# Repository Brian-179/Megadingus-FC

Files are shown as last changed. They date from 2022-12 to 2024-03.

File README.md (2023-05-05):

# Megadingus-FC
Megadingus flight controllers/altimeters

(OUTDATED) FC1.5: Mostly tested, i2C bus is having an error, SPI untested and UART/USB works fine.

FC2.1: Fully ground tested but not flight proven under TVC. TVC flight imminent.

3 pyro channels

WiFi (ESP8266)

Main MCU is an RP2040

Main power connector is an XT30 (2-5S, 6S if you're willing to take the risk)

USB Mini B port

BMI088 IMU, BME280 Barometer

3 servo outputs

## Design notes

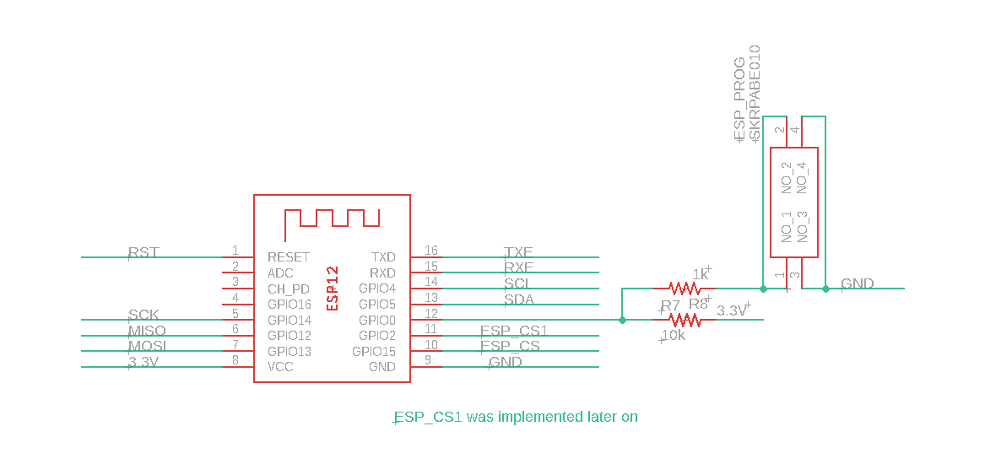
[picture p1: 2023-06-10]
fc2.1/fc2.1_8266/Screenshot 2023-06-04 113441.png

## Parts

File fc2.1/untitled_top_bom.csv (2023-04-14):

Comment | Designator | Footprint | LCSC Part #
ABLS-12.000MHZ-B4-T | F1 | HC/49US-(AT49)_1
ASMB-KTF0-0A306 | LED1 | ASMBKTF00A306
BME280 | HM1 | BME280
BMI088 | IC2 | BMI088
GDH04S04 | S1 | SOIC127P813X256-8N
L7805CDT-TR | IC5 | L7805CDTTR
RP2040 | U1 | QFN-56
SKRPABE010 | ESP_PROG RP2040-PROG RST | SKRPABE010

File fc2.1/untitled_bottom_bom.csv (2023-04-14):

Comment | Designator | Footprint | LCSC Part #
0 | R12 R14 R16 R17 | R2512
1k | R3 R6 R8 R10 | M0805
1uf | C6 | C0805
10k | R4 R5 R7 R9 R11 R13 R15 | M0805
10uf | C1 C5 | C0805
27p | C2 C3 | C0805
30 | R18 | M0805
33 | R1 R2 | M0805
47 | R19 | M0805
100 | R20 | M0805
503398-1892 | J1 | 503398-1892
FT231XS-R | IC3 | SOP64P599X175-20N
SISH536DN-T1-GE3 | Q1 Q2 Q5 | SQSA80ENWT1_GE3
TC1264-3.3VDBTR | IC1 | SOT230P700X180-4N
W25Q128JVSIQ_TR | L1 L2 | SOIC127P780X195-8N

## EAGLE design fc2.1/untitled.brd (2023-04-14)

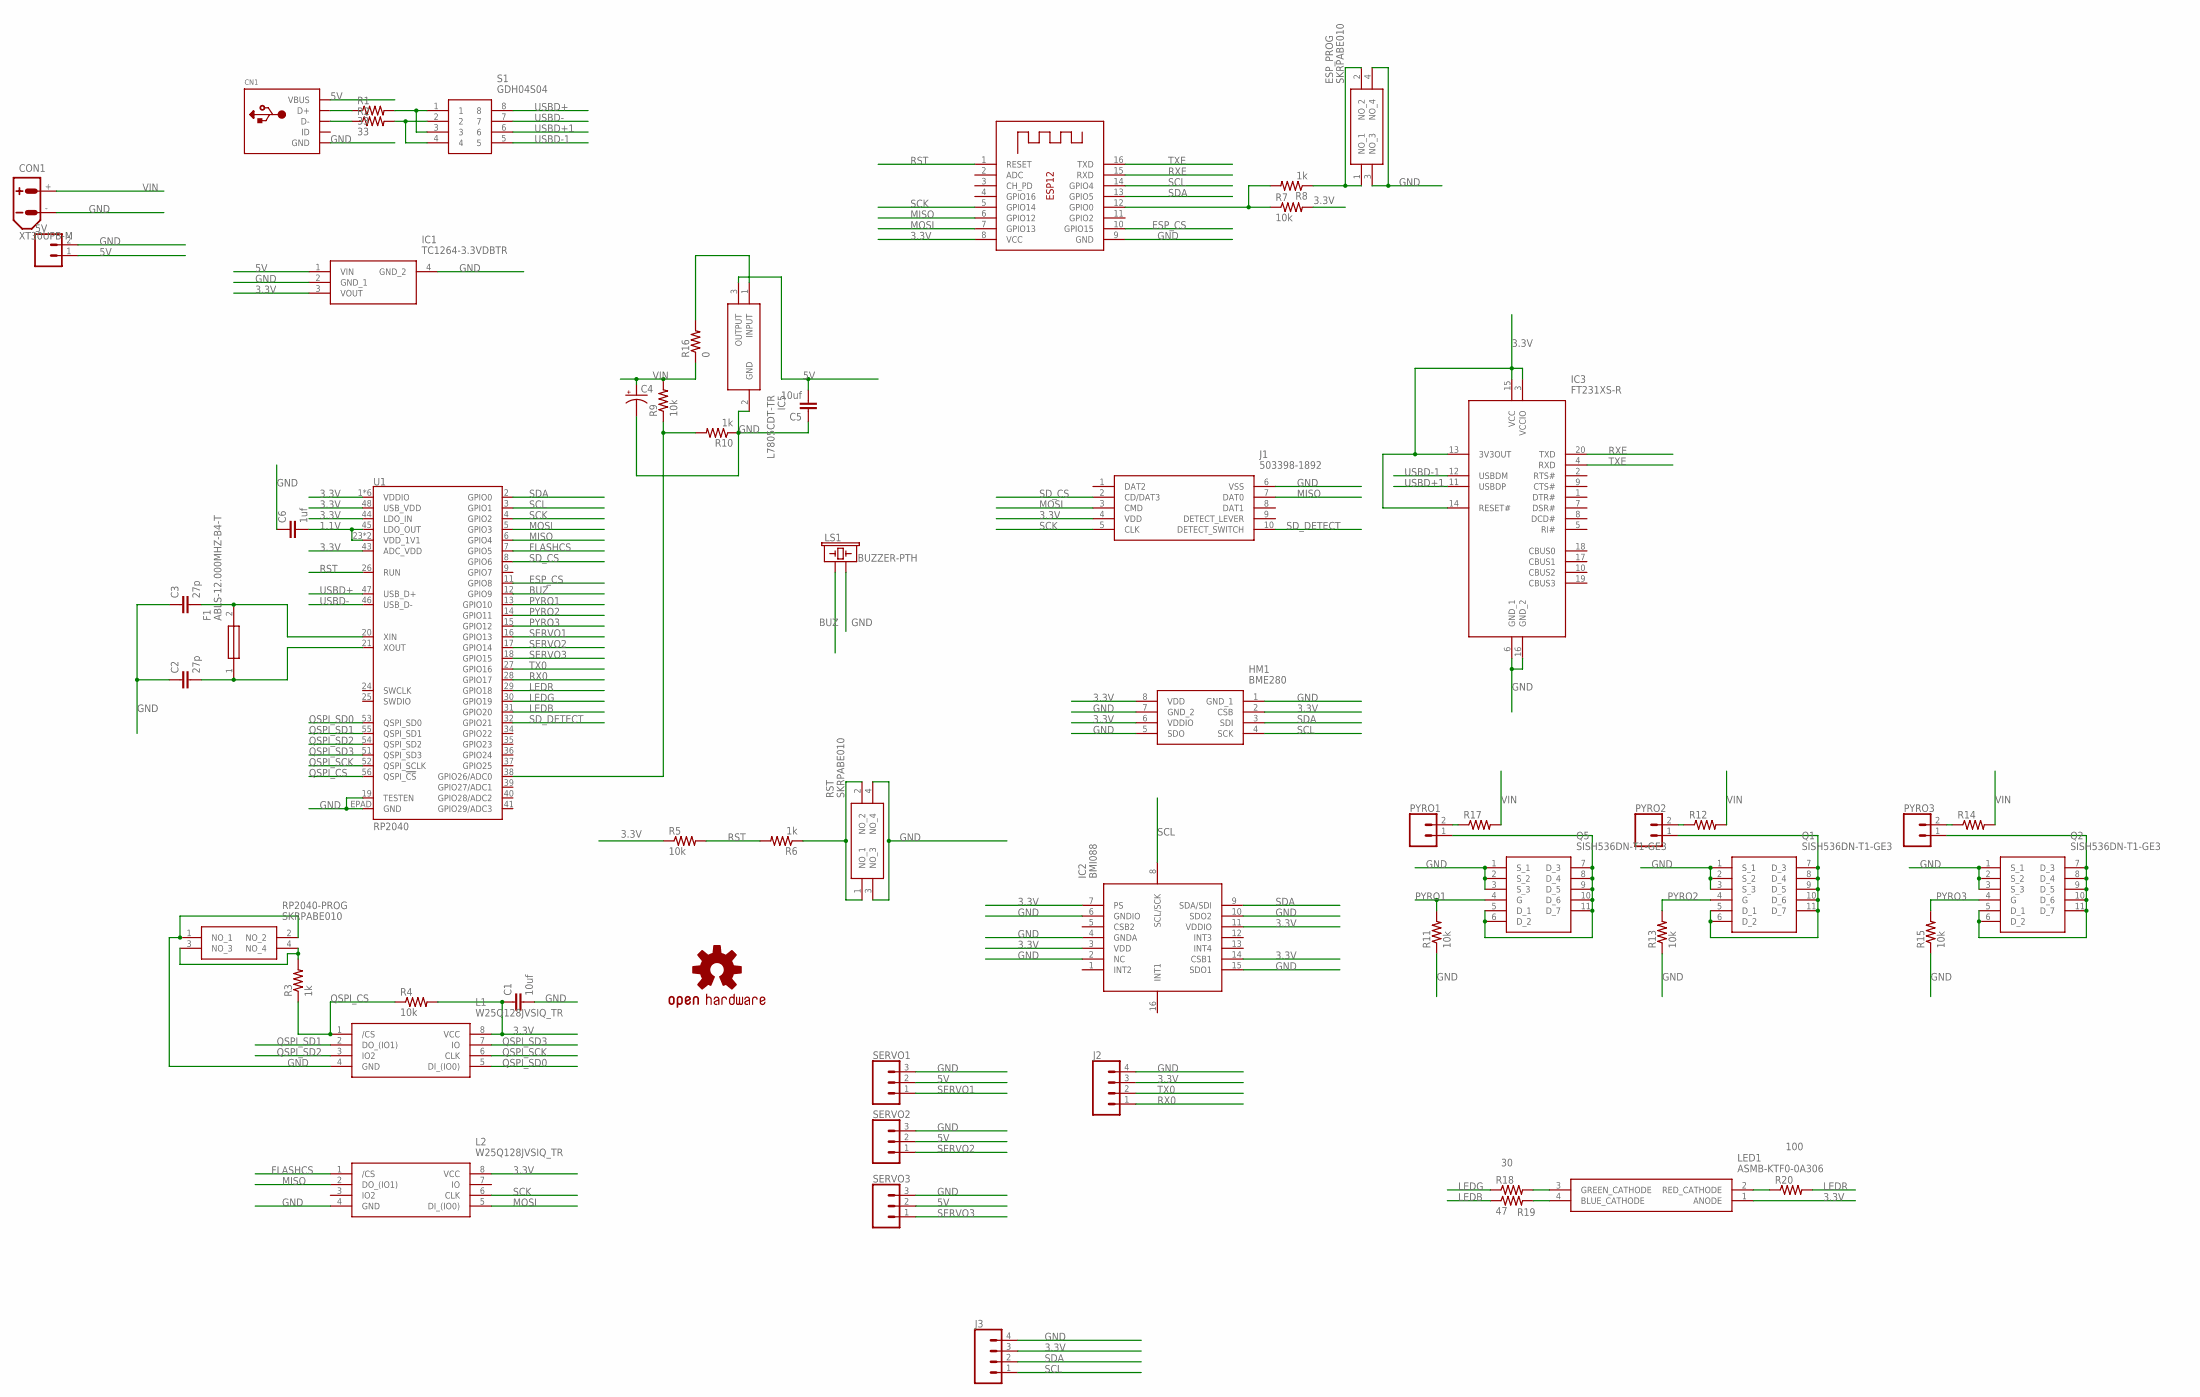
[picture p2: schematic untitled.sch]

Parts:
5V: CONN_02; 1X02
C1, C5: 10uf; C0805
C2, C3: 27p; C0805
C4: CPOL-USE3.5-8; E3,5-8
C6: 1uf; C0805
CN1: USBMINIB; USB-MINIB
CON1: XT30UPB-M
ESP_PROG: SKRPABE010
F1: ABLS-12.000MHZ-B4-T; HC/49US-(AT49)_1
HM1: BME280
IC1: TC1264-3.3VDBTR; SOT230P700X180-4N
IC2: BMI088
IC3: FT231XS-R; SOP64P599X175-20N
IC5: L7805CDT-TR; L7805CDTTR
J1: 503398-1892
J2, J3: CONN_04; 1X04
L1, L2: W25Q128JVSIQ_TR; SOIC127P780X195-8N
LED1: ASMB-KTF0-0A306; ASMBKTF00A306
LOGO1: OSHW-LOGOS; OSHW-LOGO-S
LS1: BUZZER-PTH; BUZZER-12MM
PYRO1, PYRO2, PYRO3: CONN_025MM; SCREWTERMINAL-5MM-2
Q1, Q2, Q5: SISH536DN-T1-GE3; SQSA80ENWT1_GE3
R1, R2: 33; M0805
R3, R6, R8, R10: 1k; M0805
R4, R5, R7, R9, R11, R13, R15: 10k; M0805
R12, R14, R16, R17: 0; R2512
R18: 30; M0805
R19: 47; M0805
R20: 100; M0805
RP2040-PROG: SKRPABE010
RST: SKRPABE010
S1: GDH04S04; SOIC127P813X256-8N
SERVO1, SERVO2, SERVO3: CONN_03; 1X03
U1: RP2040; QFN-56
X1: ESP-12

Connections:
1.1V: C6.2, U1.23 (VDD_1V1), U1.45 (LDO_OUT), U1.50 (VDD_1V1)
3.3V: C1.1, HM1.2 (CSB), HM1.6 (VDDIO), HM1.8 (VDD), IC1.3 (VOUT), IC2.3 (VDD), IC2.7 (PS), IC2.11 (VDDIO), IC2.14 (CSB1), IC3.3 (VCCIO), IC3.13 (3V3OUT), IC3.14 (RESET#), IC3.15 (VCC), J1.4 (VDD), J2.3, J3.3, L1.8 (VCC), L2.8 (VCC), LED1.1 (ANODE), R4.2, R5.1, R7.2, U1.1 (VDDIO), U1.10 (VDDIO), U1.22 (VDDIO), U1.33 (VDDIO), U1.42 (VDDIO), U1.43 (ADC_VDD), U1.44 (LDO_IN), U1.48 (USB_VDD), U1.49 (VDDIO), X1.8 (VCC)
5V: 5V.1, C5.2, CN1.VBUS, IC1.1 (VIN), IC5.3 (OUTPUT), SERVO1.2, SERVO2.2, SERVO3.2
BUZ: LS1.+ (1), U1.12 (GPIO9)
ESP_CS: U1.11 (GPIO8), X1.10 (GPIO15)
FLASHCS: L2.1 (/CS), U1.7 (GPIO5)
GND: 5V.2, C1.2, C2.1, C3.1, C4.-, C5.1, C6.1, CN1.GND, CON1.-, ESP_PROG.3 (NO_3), ESP_PROG.4 (NO_4), HM1.1 (GND_1), HM1.5 (SDO), HM1.7 (GND_2), IC1.2 (GND_1), IC1.4 (GND_2), IC2.2 (NC), IC2.4 (GNDA), IC2.6 (GNDIO), IC2.10 (SDO2), IC2.15 (SDO1), IC3.6 (GND_1), IC3.16 (GND_2), IC5.2 (GND), J1.6 (VSS), J2.4, J3.4, L1.4 (GND), L2.4 (GND), LS1.- (2), Q1.1 (S_1), Q1.2 (S_2), Q1.3 (S_3), Q2.1 (S_1), Q2.2 (S_2), Q2.3 (S_3), Q5.1 (S_1), Q5.2 (S_2), Q5.3 (S_3), R10.1, R11.1, R13.1, R15.1, RP2040-PROG.1 (NO_1), RP2040-PROG.2 (NO_2), RST.3 (NO_3), RST.4 (NO_4), SERVO1.3, SERVO2.3, SERVO3.3, U1.19 (TESTEN), U1.EPAD (GND), X1.9 (GND)
LEDB: R19.1, U1.31 (GPIO20)
LEDG: R18.1, U1.30 (GPIO19)
LEDR: R20.2, U1.29 (GPIO18)
MISO: J1.7 (DAT0), L2.2 (DO_(IO1)), U1.6 (GPIO4), X1.6 (GPIO12)
MOSI: J1.3 (CMD), L2.5 (DI_(IO0)), U1.5 (GPIO3), X1.7 (GPIO13)
unnamed: PYRO2.2, R12.1
unnamed: R3.2, RP2040-PROG.3 (NO_3), RP2040-PROG.4 (NO_4)
unnamed: ESP_PROG.1 (NO_1), ESP_PROG.2 (NO_2), R8.1
unnamed: R6.1, RST.1 (NO_1), RST.2 (NO_2)
unnamed: CN1.D+, R1.1
unnamed: CN1.D-, R2.1
unnamed: PYRO2.1, Q1.5 (D_1), Q1.6 (D_2), Q1.7 (D_3), Q1.8 (D_4), Q1.9 (D_5), Q1.10 (D_6), Q1.11 (D_7)
unnamed: PYRO3.2, R14.1
unnamed: PYRO1.1, Q5.5 (D_1), Q5.6 (D_2), Q5.7 (D_3), Q5.8 (D_4), Q5.9 (D_5), Q5.10 (D_6), Q5.11 (D_7)
unnamed: R7.1, R8.2, X1.12 (GPIO0)
unnamed: PYRO3.1, Q2.5 (D_1), Q2.6 (D_2), Q2.7 (D_3), Q2.8 (D_4), Q2.9 (D_5), Q2.10 (D_6), Q2.11 (D_7)
unnamed: R1.2, S1.1, S1.3
unnamed: IC5.1 (INPUT), R16.2
unnamed: PYRO1.2, R17.1
unnamed: R2.2, S1.2, S1.4
unnamed: C3.2, F1.2, U1.20 (XIN)
unnamed: C2.2, F1.1, U1.21 (XOUT)
unnamed: LED1.3 (GREEN_CATHODE), R18.2
unnamed: R9.1, R10.2, U1.38 (GPIO26/ADC0)
unnamed: LED1.4 (BLUE_CATHODE), R19.2
unnamed: LED1.2 (RED_CATHODE), R20.1
PYRO1: Q5.4 (G), R11.2, U1.13 (GPIO10)
PYRO2: Q1.4 (G), R13.2, U1.14 (GPIO11)
PYRO3: Q2.4 (G), R15.2, U1.15 (GPIO12)
QSPI_CS: L1.1 (/CS), R3.1, R4.1, U1.56 (QSPI_!CS!)
QSPI_SCK: L1.6 (CLK), U1.52 (QSPI_SCLK)
QSPI_SD0: L1.5 (DI_(IO0)), U1.53 (QSPI_SD0)
QSPI_SD1: L1.2 (DO_(IO1)), U1.55 (QSPI_SD1)
QSPI_SD2: L1.3 (IO2), U1.54 (QSPI_SD2)
QSPI_SD3: L1.7 (IO), U1.51 (QSPI_SD3)
RST: R5.2, R6.2, U1.26 (RUN), X1.1 (RESET)
RX0: J2.1, U1.28 (GPIO17)
RXE: IC3.20 (TXD), X1.15 (RXD)
SCK: J1.5 (CLK), L2.6 (CLK), U1.4 (GPIO2), X1.5 (GPIO14)
SCL: HM1.4 (SCK), IC2.8 (SCL/SCK), J3.1, U1.3 (GPIO1), X1.14 (GPIO4)
SDA: HM1.3 (SDI), IC2.9 (SDA/SDI), J3.2, U1.2 (GPIO0), X1.13 (GPIO5)
SD_CS: J1.2 (CD/DAT3), U1.8 (GPIO6)
SD_DETECT: J1.10 (DETECT_SWITCH), U1.32 (GPIO21)
SERVO1: SERVO1.1, U1.16 (GPIO13)
SERVO2: SERVO2.1, U1.17 (GPIO14)
SERVO3: SERVO3.1, U1.18 (GPIO15)
TX0: J2.2, U1.27 (GPIO16)
TXE: IC3.4 (RXD), X1.16 (TXD)
USBD+: S1.8, U1.47 (USB_D+)
USBD+1: IC3.11 (USBDP), S1.6
USBD-: S1.7, U1.46 (USB_D-)
USBD-1: IC3.12 (USBDM), S1.5
VIN: C4.+, CON1.+, R9.2, R12.2, R14.2, R16.1, R17.2

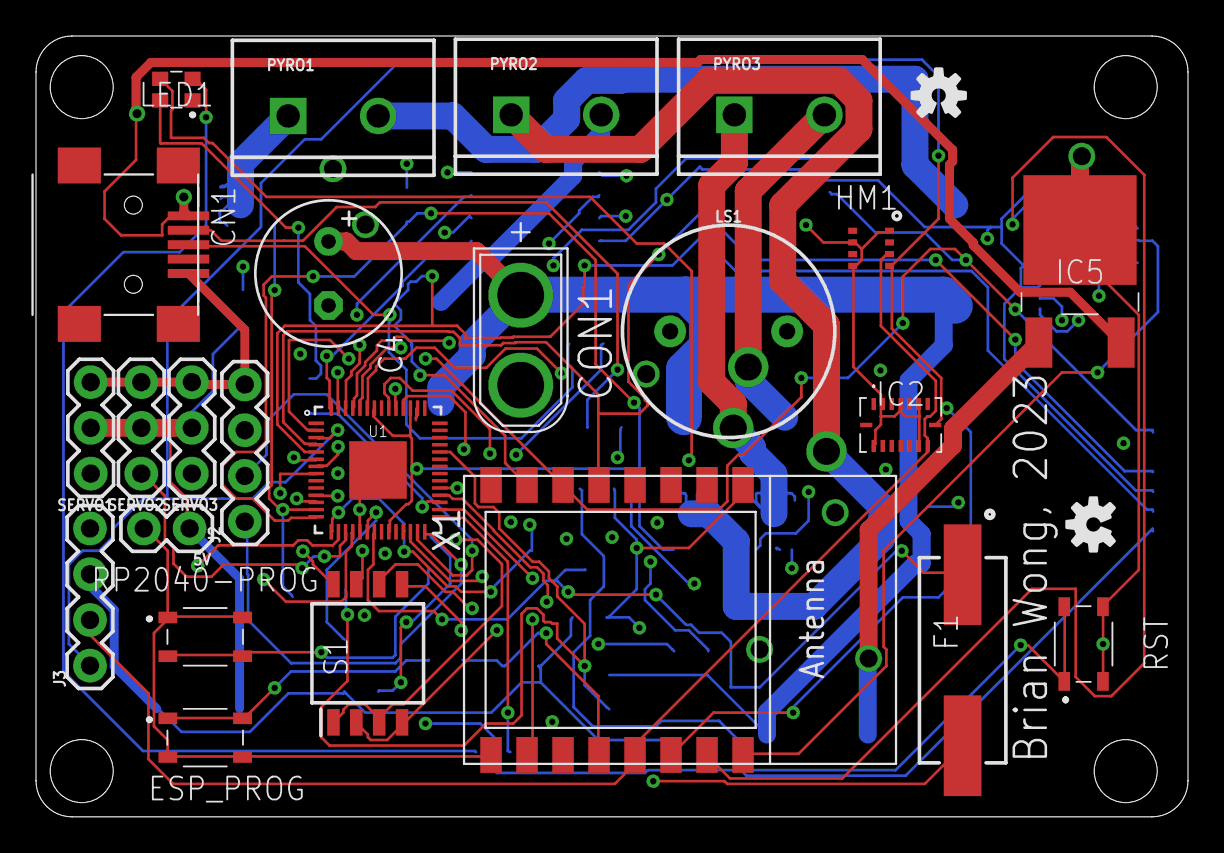
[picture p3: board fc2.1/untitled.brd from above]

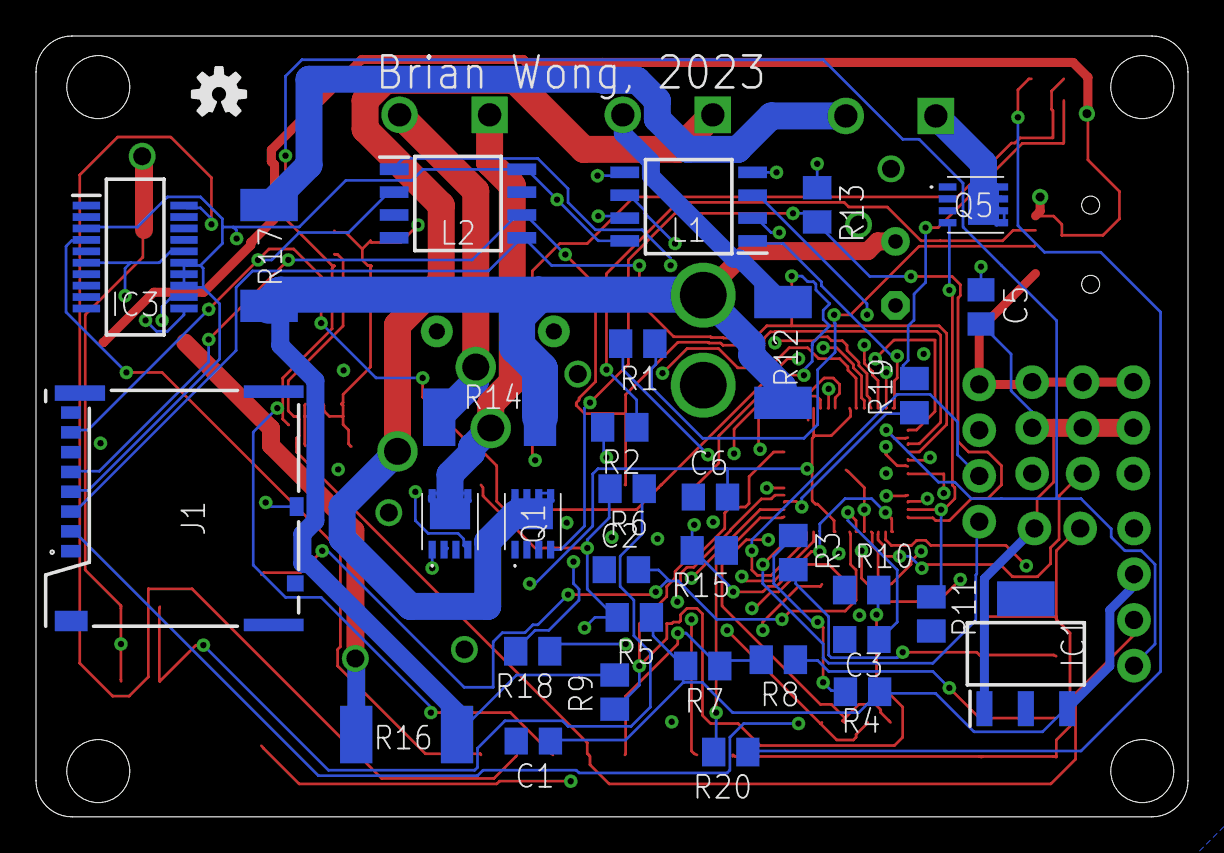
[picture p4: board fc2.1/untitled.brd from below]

Board: 4 copper layers, 64.0 x 43.4 mm, 60 parts (34 on the bottom side), 60 nets.

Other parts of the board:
LOGO2, LOGO3: OSHW-LOGOS; OSHW-LOGO-S

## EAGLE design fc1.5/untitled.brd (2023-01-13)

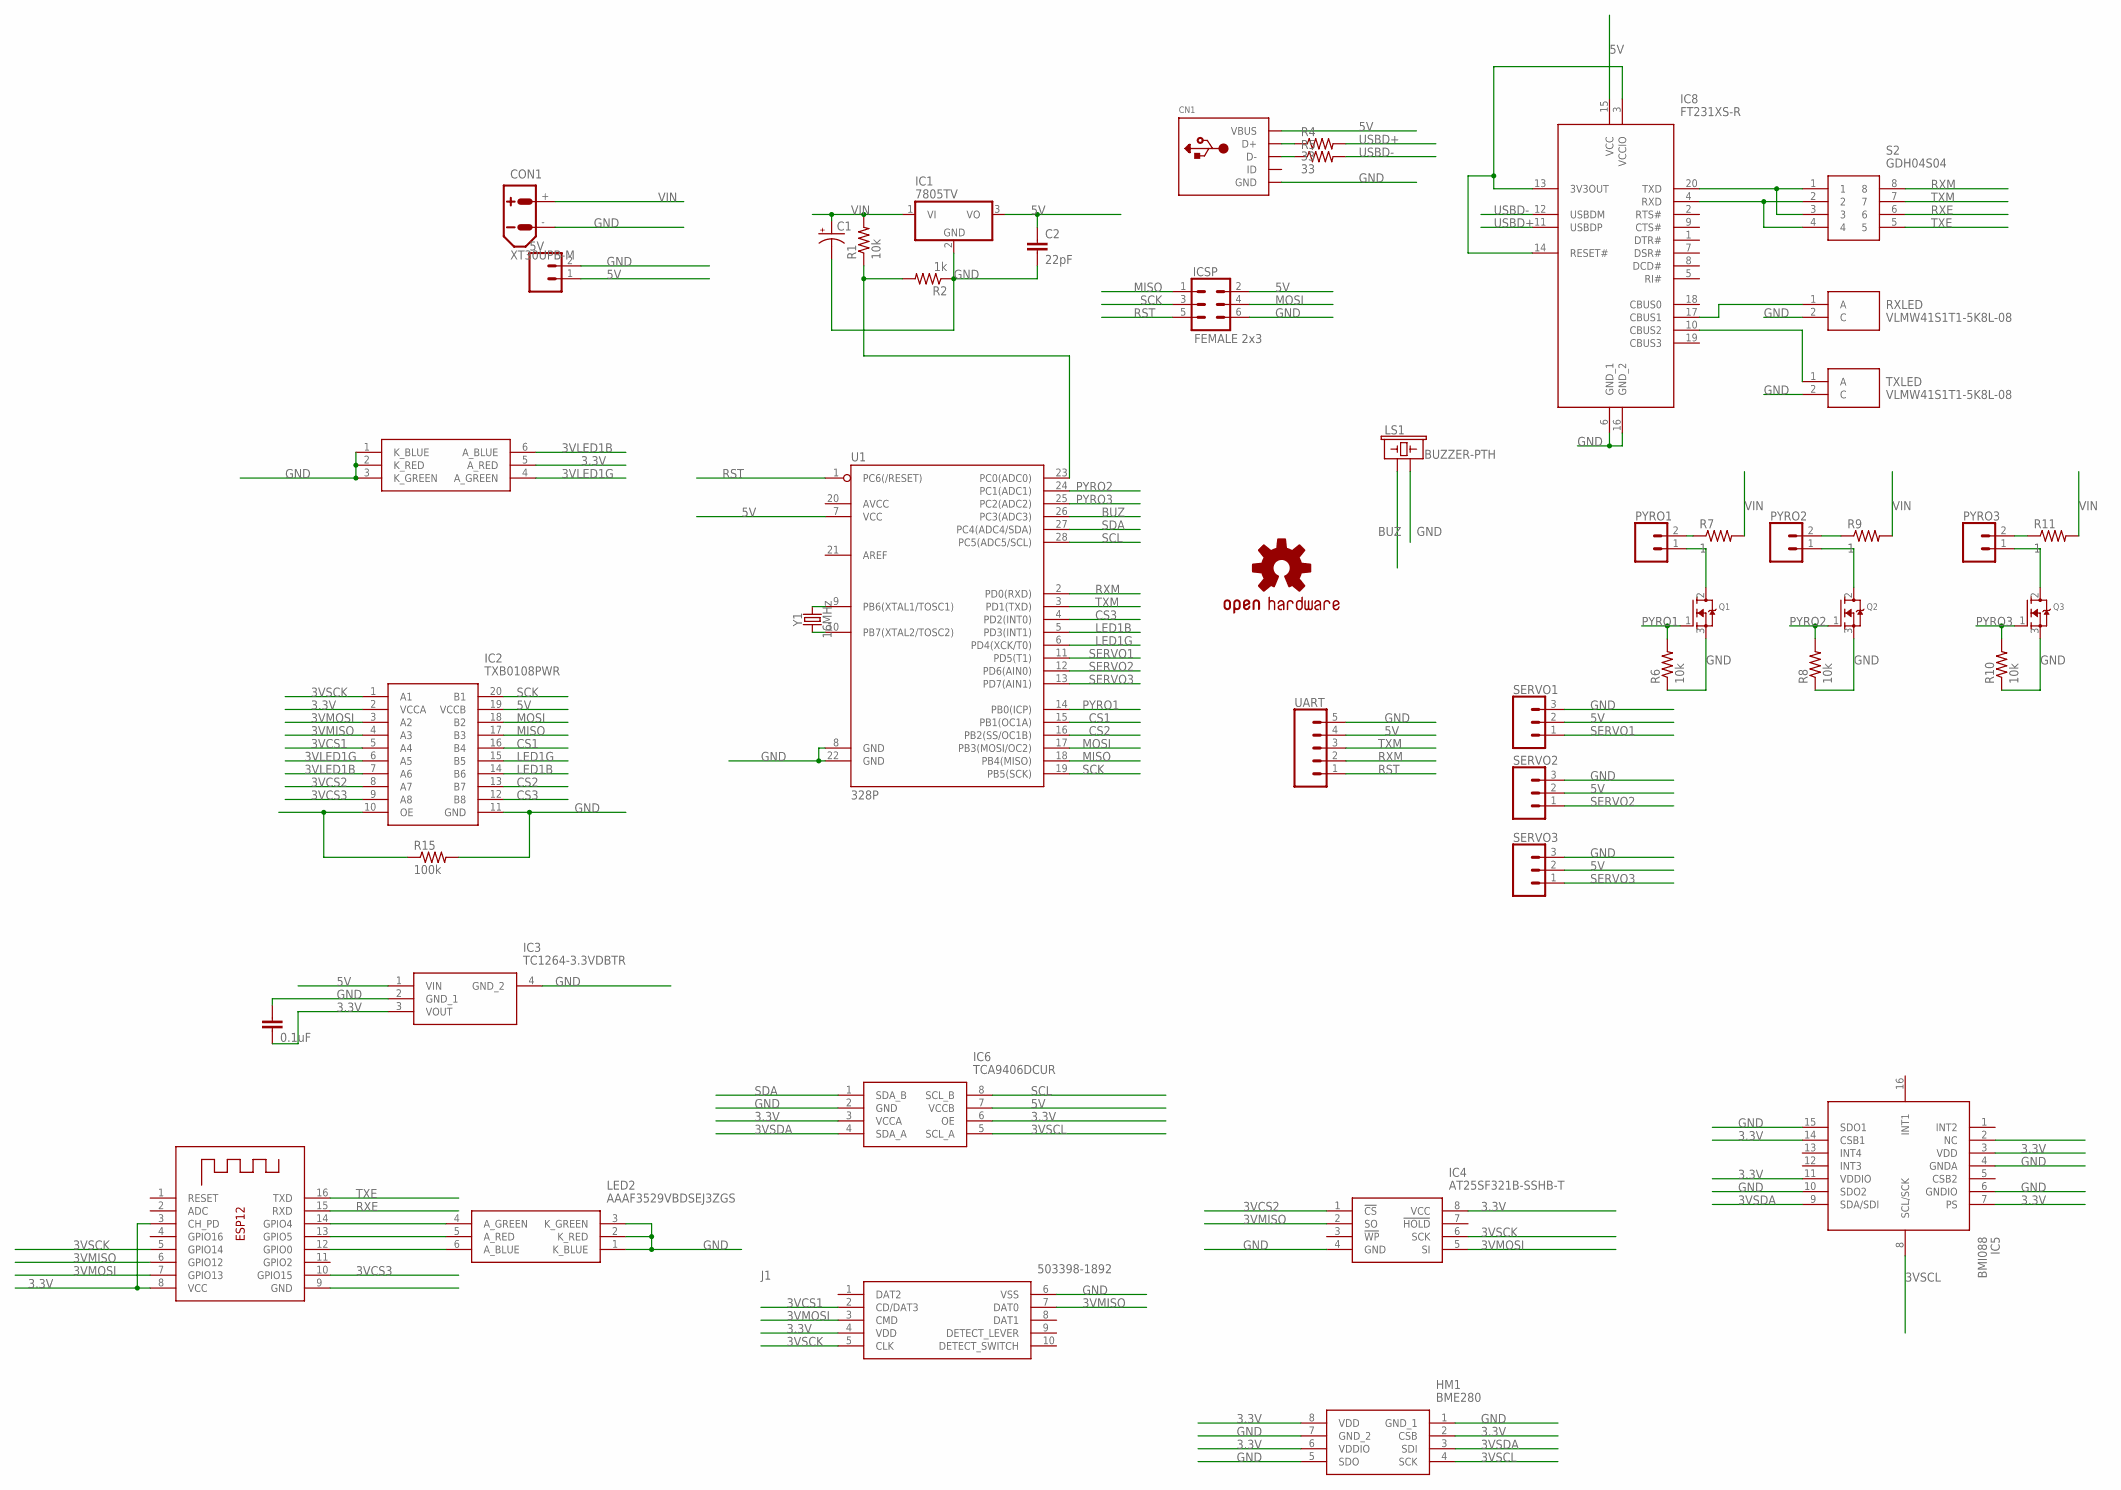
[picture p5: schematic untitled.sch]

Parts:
5V: CONN_02; 1X02
C1: CPOL-USE3.5-8; E3,5-8
C2: 22pF; CAP-PTH-2.54
C4: 0.1uF; CAP-PTH-SMALL-KIT
CN1: USBMINIB; USB-MINIB
CON1: XT30UPB-M
HM1: BME280
IC1: 7805TV; TO220V
IC2: TXB0108PWR; SOP65P640X120-20N
IC3: TC1264-3.3VDBTR; SOT230P700X180-4N
IC4: AT25SF321B-SSHB-T; SOIC127P600X175-8N
IC5: BMI088
IC6: TCA9406DCUR; SOP50P310X90-8N
IC8: FT231XS-R; SOP64P599X175-20N
ICSP: FEMALE 2x3; 2X3
J1: 503398-1892
LED1, LED2: AAAF3529VBDSEJ3ZGS
LOGO1: OSHW-LOGOL; OSHW-LOGO-L
LS1: BUZZER-PTH; BUZZER-12MM
PYRO1, PYRO2, PYRO3: CONN_025MM; SCREWTERMINAL-5MM-2
Q1, Q2, Q3: MOSFET-NGDS_TO220V; TO220V
R1, R6, R8, R10: 10k; 0805-THM
R2: 1k; 0805-THM
R4, R5: 33; 0805-THM
R7, R9, R11: 1; 0805-THM
R15: 100k; 0805-THM
RXLED: VLMW41S1T1-5K8L-08; LEDM3528X185N
S2: GDH04S04; SOIC127P813X256-8N
SERVO1, SERVO2, SERVO3: CONN_03; 1X03
TXLED: VLMW41S1T1-5K8L-08; LEDM3528X185N
U1: 328P; DIP28
UART: CONN_05; 1X05
X1: ESP-12
Y1: 16MHz; HC49US

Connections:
3.3V: C4.2, HM1.2 (CSB), HM1.6 (VDDIO), HM1.8 (VDD), IC2.2 (VCCA), IC3.3 (VOUT), IC4.8 (VCC), IC5.3 (VDD), IC5.7 (PS), IC5.11 (VDDIO), IC5.14 (CSB1), IC6.3 (VCCA), IC6.6 (OE), J1.4 (VDD), LED1.5 (A_RED), X1.3 (CH_PD), X1.8 (VCC)
3VCS1: IC2.5 (A4), J1.2 (CD/DAT3)
3VCS2: IC2.8 (A7), IC4.1 (!CS)
3VCS3: IC2.9 (A8), X1.10 (GPIO15)
3VLED1B: IC2.7 (A6), LED1.6 (A_BLUE)
3VLED1G: IC2.6 (A5), LED1.4 (A_GREEN)
3VMISO: IC2.4 (A3), IC4.2 (SO), J1.7 (DAT0), X1.6 (GPIO12)
3VMOSI: IC2.3 (A2), IC4.5 (SI), J1.3 (CMD), X1.7 (GPIO13)
3VSCK: IC2.1 (A1), IC4.6 (SCK), J1.5 (CLK), X1.5 (GPIO14)
3VSCL: HM1.4 (SCK), IC5.8 (SCL/SCK), IC6.5 (SCL_A)
3VSDA: HM1.3 (SDI), IC5.9 (SDA/SDI), IC6.4 (SDA_A)
5V: 5V.1, C2.1, CN1.VBUS, IC1.3 (VO), IC2.19 (VCCB), IC3.1 (VIN), IC6.7 (VCCB), IC8.15 (VCC), ICSP.2, SERVO1.2, SERVO2.2, SERVO3.2, U1.7 (VCC), UART.4
BUZ: LS1.+ (1), U1.26 (PC3(ADC3))
CS1: IC2.16 (B4), U1.15 (PB1(OC1A))
CS2: IC2.13 (B7), U1.16 (PB2(SS/OC1B))
CS3: IC2.12 (B8), U1.4 (PD2(INT0))
GND: 5V.2, C1.-, C2.2, C4.1, CN1.GND, CON1.-, HM1.1 (GND_1), HM1.5 (SDO), HM1.7 (GND_2), IC1.2 (GND), IC2.11 (GND), IC3.2 (GND_1), IC3.4 (GND_2), IC4.4 (GND), IC5.4 (GNDA), IC5.6 (GNDIO), IC5.10 (SDO2), IC5.15 (SDO1), IC6.2 (GND), IC8.6 (GND_1), IC8.16 (GND_2), ICSP.6, J1.6 (VSS), LED1.1 (K_BLUE), LED1.2 (K_RED), LED1.3 (K_GREEN), LED2.1 (K_BLUE), LED2.2 (K_RED), LED2.3 (K_GREEN), LS1.- (2), Q1.3 (S), Q2.3 (S), Q3.3 (S), R2.1, R6.1, R8.1, R10.1, R15.2, RXLED.2 (C), SERVO1.3, SERVO2.3, SERVO3.3, TXLED.2 (C), U1.8 (GND), U1.22 (GND), UART.5, X1.9 (GND)
LED1B: IC2.14 (B6), U1.5 (PD3(INT1))
LED1G: IC2.15 (B5), U1.6 (PD4(XCK/T0))
MISO: IC2.17 (B3), ICSP.1, U1.18 (PB4(MISO))
MOSI: IC2.18 (B2), ICSP.4, U1.17 (PB3(MOSI/OC2))
unnamed: U1.9 (PB6(XTAL1/TOSC1)), Y1.2
unnamed: U1.10 (PB7(XTAL2/TOSC2)), Y1.1
unnamed: R1.1, R2.2, U1.23 (PC0(ADC0))
unnamed: CN1.D+, R4.1
unnamed: IC8.17 (CBUS1), RXLED.1 (A)
unnamed: IC8.20 (TXD), S2.1, S2.3
unnamed: IC8.4 (RXD), S2.2, S2.4
unnamed: IC8.3 (VCCIO), IC8.13 (3V3OUT), IC8.14 (RESET#)
unnamed: CN1.D-, R5.1
unnamed: IC8.10 (CBUS2), TXLED.1 (A)
unnamed: LED2.4 (A_GREEN), X1.14 (GPIO4)
unnamed: LED2.5 (A_RED), X1.13 (GPIO5)
unnamed: IC2.10 (OE), R15.1
unnamed: PYRO1.1, Q1.2 (D)
unnamed: PYRO1.2, R7.1
unnamed: PYRO2.1, Q2.2 (D)
unnamed: PYRO2.2, R9.1
unnamed: PYRO3.1, Q3.2 (D)
unnamed: PYRO3.2, R11.1
unnamed: LED2.6 (A_BLUE), X1.12 (GPIO0)
PYRO1: Q1.1 (G), R6.2, U1.14 (PB0(ICP))
PYRO2: Q2.1 (G), R8.2, U1.24 (PC1(ADC1))
PYRO3: Q3.1 (G), R10.2, U1.25 (PC2(ADC2))
RST: ICSP.5, U1.1 (PC6(/RESET)), UART.1
RXE: S2.6, X1.15 (RXD)
RXM: S2.8, U1.2 (PD0(RXD)), UART.2
SCK: IC2.20 (B1), ICSP.3, U1.19 (PB5(SCK))
SCL: IC6.8 (SCL_B), U1.28 (PC5(ADC5/SCL))
SDA: IC6.1 (SDA_B), U1.27 (PC4(ADC4/SDA))
SERVO1: SERVO1.1, U1.11 (PD5(T1))
SERVO2: SERVO2.1, U1.12 (PD6(AIN0))
SERVO3: SERVO3.1, U1.13 (PD7(AIN1))
TXE: S2.5, X1.16 (TXD)
TXM: S2.7, U1.3 (PD1(TXD)), UART.3
USBD+: IC8.11 (USBDP), R4.2
USBD-: IC8.12 (USBDM), R5.2
VIN: C1.+, CON1.+, IC1.1 (VI), R1.2, R7.2, R9.2, R11.2

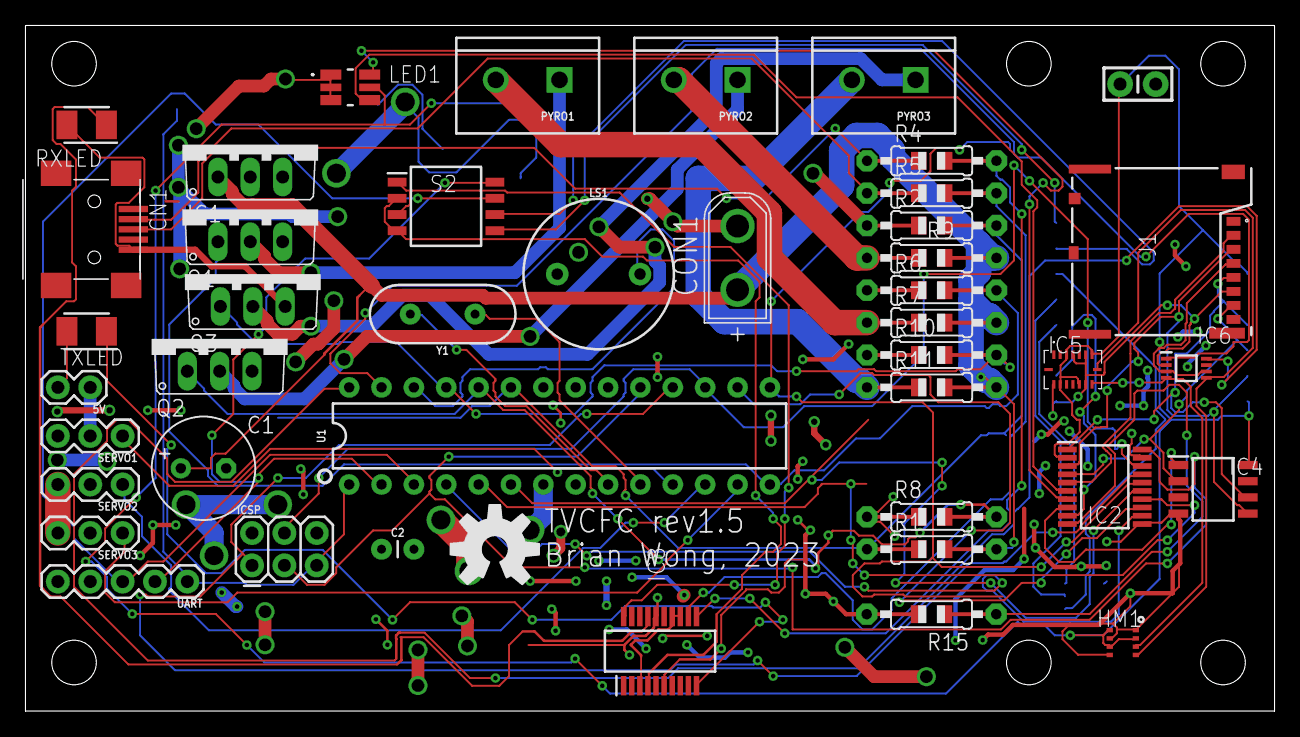
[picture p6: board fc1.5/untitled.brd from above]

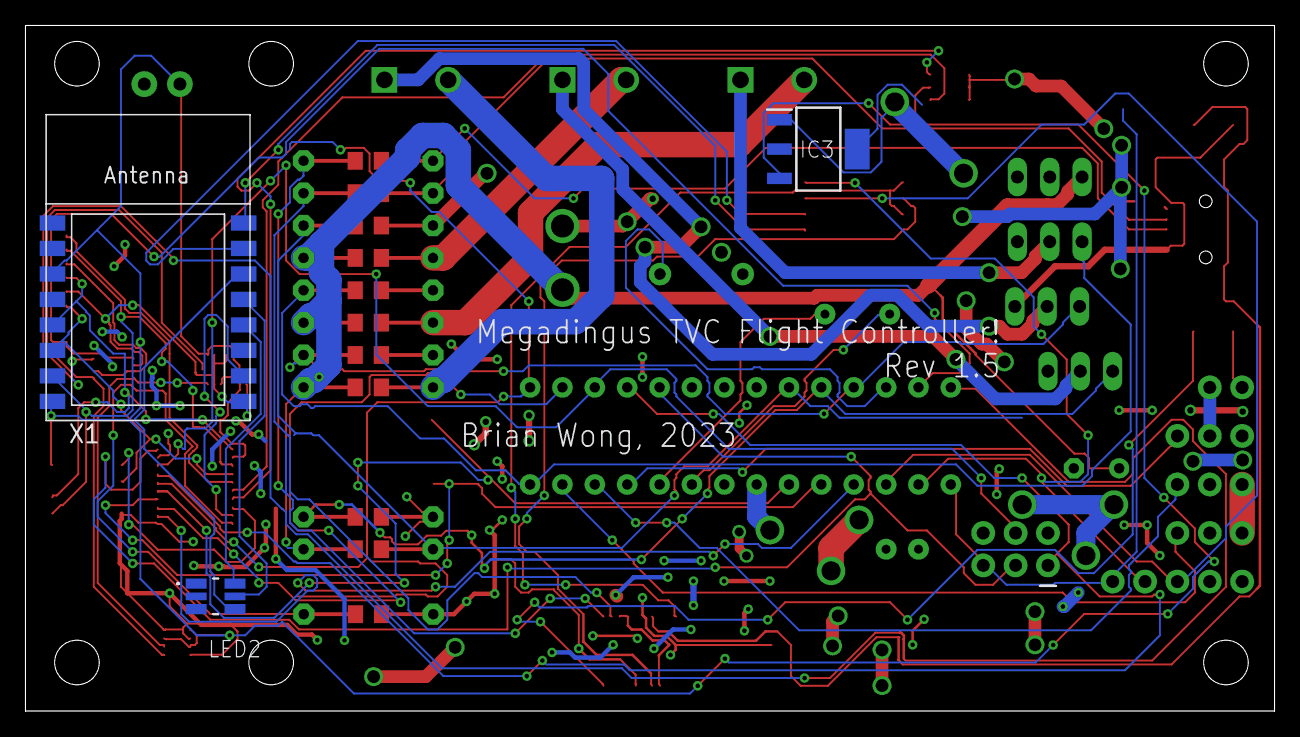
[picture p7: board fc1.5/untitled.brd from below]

Board: 2 copper layers, 98.0 x 53.8 mm, 47 parts (3 on the bottom side), 58 nets.

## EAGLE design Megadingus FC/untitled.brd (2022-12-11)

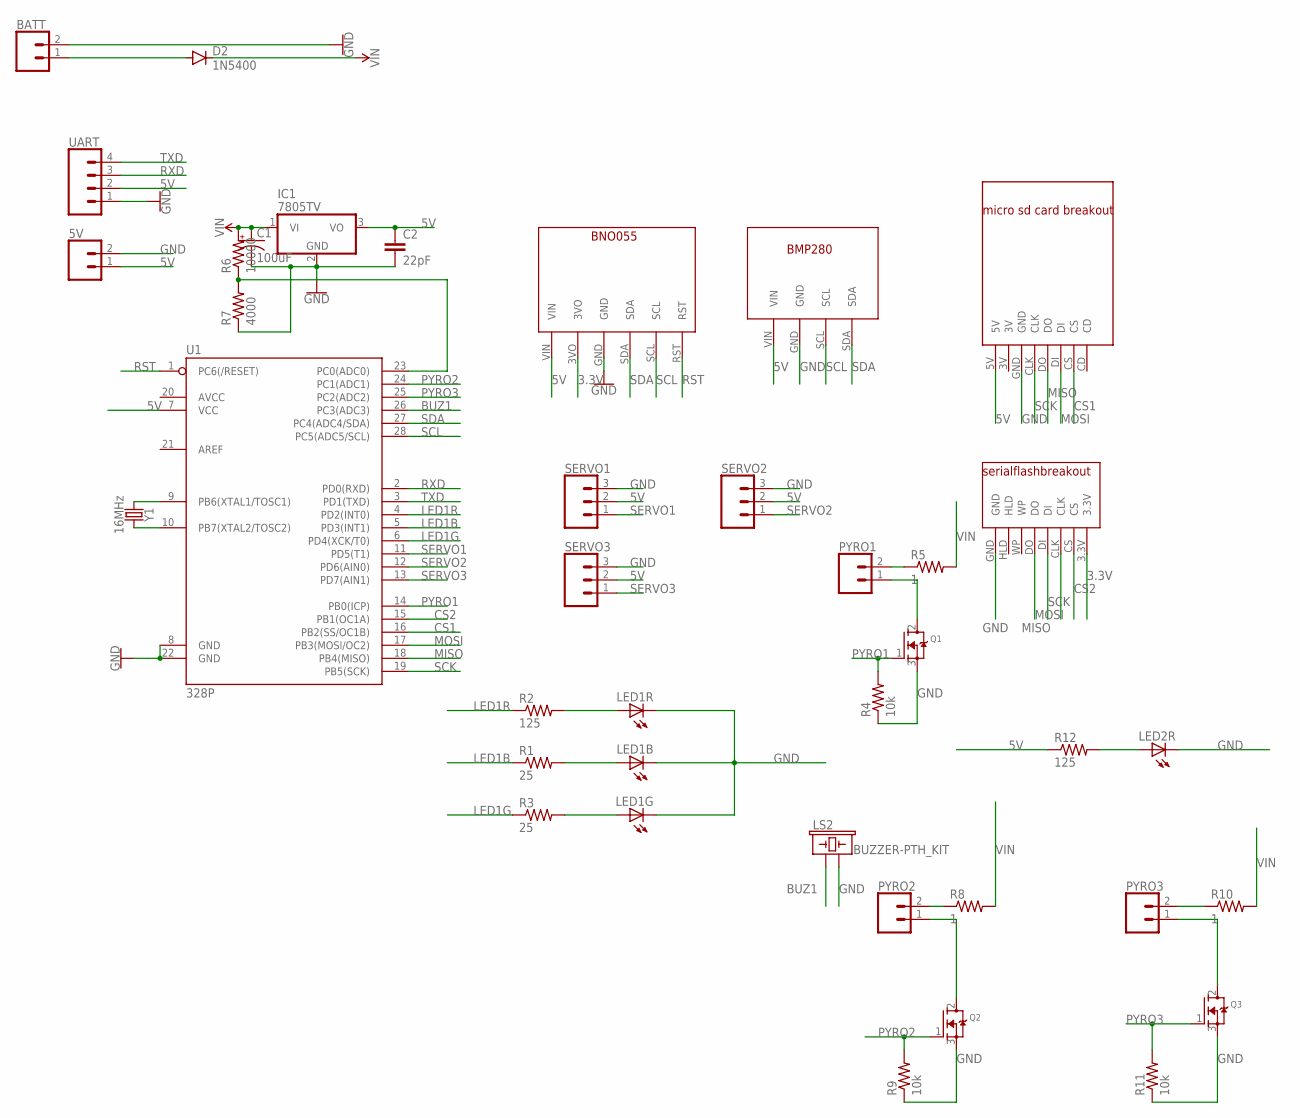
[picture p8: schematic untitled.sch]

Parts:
5V: CONN_02; 1X02
BATT: CONN_02; 1X02
C1: 100uF; CPOL-RADIAL-2.5MM-6.5MM
C2: 22pF; CAP-PTH-2.54
D2: 1N5400; DO201-15
IC1: 7805TV; TO220V
LED1B: LED1B; LED5MM
LED1G: LED1G; LED5MM
LED1R, LED2R: LED1R; LED5MM
LS2: BUZZER-PTH_KIT; BUZZER-12MM-KIT
PYRO1, PYRO2, PYRO3: CONN_02; 1X02
Q1, Q2, Q3: MOSFET-NGDS_TO220V; TO220V
R1, R3: 25; 0805-THM
R2, R12: 125; 0805-THM
R4, R9, R11: 10k; 0805-THM
R5, R8, R10: 1; 0805-THM
R6: 10000; 0805-THM
R7: 4000; 0805-THM
SERVO1, SERVO2, SERVO3: CONN_03; 1X03
U1: 328P; DIP28
U$1: BNO055
U$2: BMP280
U$3: ADAFRUITSDCARD
U$4: SPARKFUNFLASHBREAKOUT
UART: CONN_04PTH; 1X04
Y1: 16MHz; HC49US

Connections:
3.3V: U$1.3VO, U$4.3.3V
5V: 5V.1, C2.1, IC1.3 (VO), R12.1, SERVO1.2, SERVO2.2, SERVO3.2, U1.7 (VCC), U$1.VIN, U$2.VIN, U$3.5V, UART.2
BUZ1: LS2.+ (1), U1.26 (PC3(ADC3))
CS1: U1.16 (PB2(SS/OC1B)), U$3.CS
CS2: U1.15 (PB1(OC1A)), U$4.CS
GND: 5V.2, BATT.2, C1.2 (-), C2.2, IC1.2 (GND), LED1B.K (C), LED1G.K (C), LED1R.K (C), LED2R.K (C), LS2.- (2), Q1.3 (S), Q2.3 (S), Q3.3 (S), R4.1, R7.1, R9.1, R11.1, SERVO1.3, SERVO2.3, SERVO3.3, U1.8 (GND), U1.22 (GND), U$1.GND, U$2.GND, U$3.GND, U$4.GND, UART.1
LED1B: R1.1, U1.5 (PD3(INT1))
LED1G: R3.1, U1.6 (PD4(XCK/T0))
LED1R: R2.1, U1.4 (PD2(INT0))
MISO: U1.18 (PB4(MISO)), U$3.DO, U$4.DO
MOSI: U1.17 (PB3(MOSI/OC2)), U$3.DI, U$4.DI
unnamed: PYRO1.1, Q1.2 (D)
unnamed: LED1R.A, R2.2
unnamed: LED1B.A, R1.2
unnamed: LED1G.A, R3.2
unnamed: PYRO1.2, R5.1
unnamed: R6.1, R7.2, U1.23 (PC0(ADC0))
unnamed: U1.9 (PB6(XTAL1/TOSC1)), Y1.1
unnamed: U1.10 (PB7(XTAL2/TOSC2)), Y1.2
unnamed: BATT.1, D2.A
unnamed: PYRO2.2, R8.1
unnamed: PYRO3.2, R10.1
unnamed: PYRO2.1, Q2.2 (D)
unnamed: PYRO3.1, Q3.2 (D)
unnamed: LED2R.A, R12.2
PYRO1: Q1.1 (G), R4.2, U1.14 (PB0(ICP))
PYRO2: Q2.1 (G), R9.2, U1.24 (PC1(ADC1))
PYRO3: Q3.1 (G), R11.2, U1.25 (PC2(ADC2))
RST: U1.1 (PC6(/RESET)), U$1.RST
RXD: U1.2 (PD0(RXD)), UART.3
SCK: U1.19 (PB5(SCK)), U$3.CLK, U$4.CLK
SCL: U1.28 (PC5(ADC5/SCL)), U$1.SCL, U$2.SCL
SDA: U1.27 (PC4(ADC4/SDA)), U$1.SDA, U$2.SDA
SERVO1: SERVO1.1, U1.11 (PD5(T1))
SERVO2: SERVO2.1, U1.12 (PD6(AIN0))
SERVO3: SERVO3.1, U1.13 (PD7(AIN1))
TXD: U1.3 (PD1(TXD)), UART.4
VIN: C1.1 (+), D2.C, IC1.1 (VI), R5.2, R6.2, R8.2, R10.2

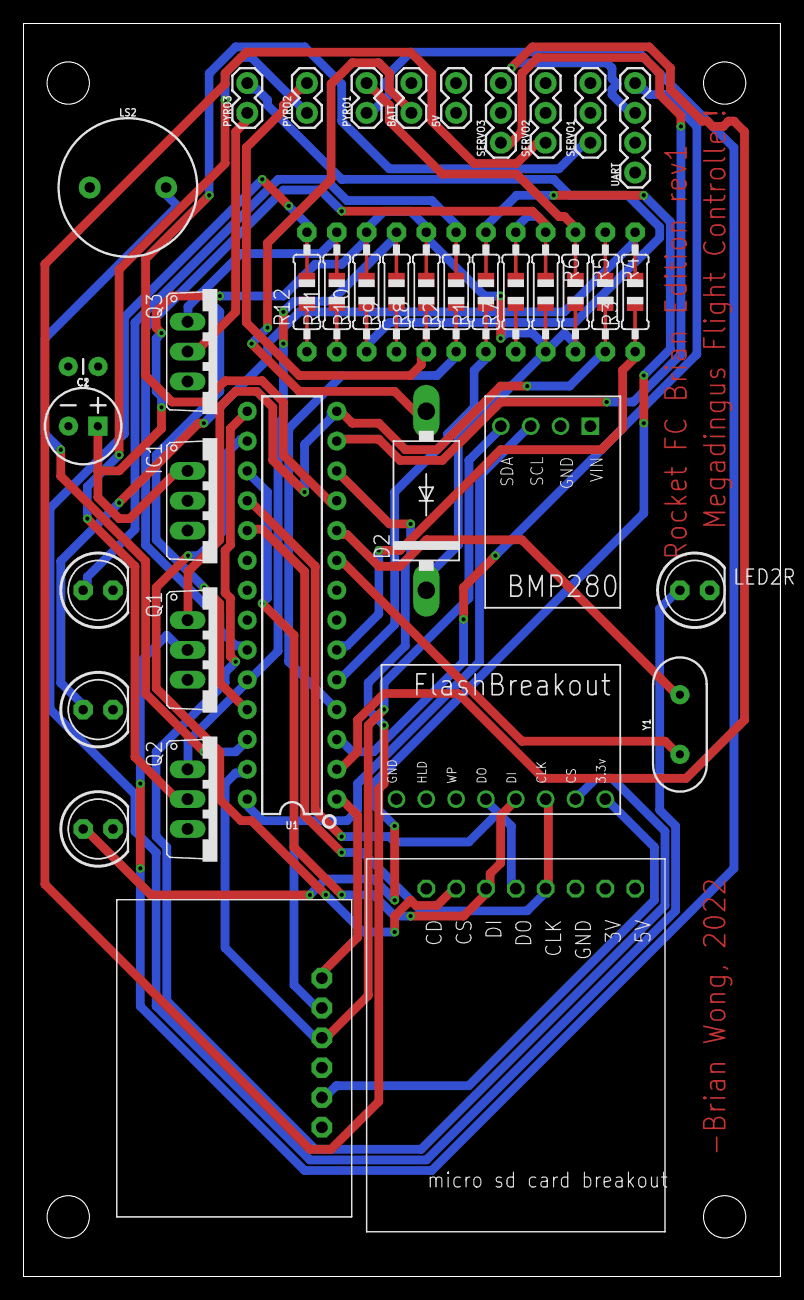
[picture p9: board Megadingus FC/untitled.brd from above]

Board: 2 copper layers, 64.4 x 106.7 mm, 39 parts (0 on the bottom side), 38 nets.

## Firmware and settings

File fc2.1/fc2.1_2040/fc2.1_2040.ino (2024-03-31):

//for Brian Wong's FC2.1 TVC Flight controller, compile for RP2040/raspberry pi pico (Earle Philhower).
//"generic RP2040"
//16mb flash, 8mb sketch 8mb FS
//W25Q128JV QSPI /4

//pyros are gpio10-12
//servos are gpio13-15
//tx and rx 0 are on gpio16 and 17 respectively
//rgb led is on gpio18-20
//buzzer is on gpio9
//esp_cs is on gpio8
//sd_cs is on gpio6
//flashcs is on gpio5
//sd_detect is on gpio25
//vin is on gpio26/adc0

//Kp is divided by 1000, for the sake of easy tuning

//4096B = ~34s of altitude datalogging.

//TODO: low pass filter for gyro (maybe accel) typedef struct for telemetry, new AHRS system, cleaning up code, config via sd card and usb serial, fix reading vin, tvc gimbal axis inversion
//The SD library in the rp2040 thing can conflict with the adafruit fork of SdFat, thus causing a failure to compile.

#include "SD.h"
//#include <SoftwareSerial.h>
#include "telem.h"

SPITelem ESP(8);
//SoftwareSerialOneWire ESPSerial(8, 38400);

//SoftwareSerial ESPSerial(4, 3); //7,8

const boolean useProp = false;
const boolean groundTest = false; //static holddown test
const boolean useParachuteServo = false; //use servo output 3 for deploying parachute (pyro channels will still be activated accordingly)

const boolean copyToSD = false; //copy datalog from internal QSPI flash to MicroSD card once landed
const boolean copyToFlash = false; //copy datalog from microSD card to internal QSPI flash once landed

boolean logToFlash = false; //datalogging to internal QSPI flash. Can cause spikes of latency in both cores; LittleFS halts both cores to write to flash. Logging to other SPI flash is work in progress, that will hopefully solve this issue.
boolean logToSD = true; //datalogging to MicroSD card.
const boolean autoLogging = false; //if there is a MicroSD card, datalogging will be done to that. Otherwise, datalogging will be sent to flash. Setting this to true will override logToFlash and logToSD.

const float imuGain = 0.01; //imu fusion thing

const double defaultP = 1.00; //default PID values (execute 'defaults' in the terminal to set them, and execute 'getpids' to see current pids) Tune for your own rocket. 6:1
const double defaultI = 0.00;
const double defaultD = 0.00;

const float defaultDelay = 4.00; //default backup delay period for apogee detect

const float referencePressure = 1017.0;// hPa local QFF (official meteor-station reading)
const float outdoorTemp = 25; // °C  measured local outdoor temp.
const float barometerAltitude = 307.0;  // meters ... map readings + barometer position, mullaley NSW is 307m

const float pyroTime = 250; //pyro channel on time (ms)

const float altThreshold = 10; //minimum altitude for apogee; if the vehicle is under this altitude in coast mode, it will not detect apogee. used to prevent accidental pyro firings.
const float baroVelLaunchDetect = 999; //barometric velocity threshold for launch detect. Default 10.
const float accelLaunchDetect = 11; //acceleration threshold for launch detect

float centrepointX = 90; //servo centrepoint,usually 90 (adjust for your own setup)
float centrepointY = 90; //80 and 95 for prototype, (x and y)

float servoLimit = 45; //servo actuation limit on either side e.g. 10deg = 10deg on either side = 20deg total
float propThrust = 170; //prop's thrust for ground testing (should be enough to get control with TVC)
float propBurnTime = 5000; //prop's on time for ground testing (milliseconds)
float gimbalDemoDelayPeriod = 100; //delay period between servo movements on gimbalDemo mode and on startup


const int SDCS = 6;
const int flashCS = 5;
const int ESPCS = 8;

const int countdownTime = 10;

//int ESPBaud = 38400; //baudrate between rp2040 and esp8266

//#include <SdFat.h>
//#include "Adafruit_SPIFlash.h"
#include <LittleFS.h>
//#include <SerialFlash.h>
#include "Aflightlibs.h"
#include <MadgwickAHRS.h>
#include <hardware/flash.h>
#include "EEPROM.h"
//#include <SPIMemory.h>
//#include <PID_v1.h>
#include <SPI.h>
//#include <SDFS.h>
#include <Servo.h>
#include "BMI088.h"
//#include "SPIFlash.h"
#include "Arduino.h"
//#include "SdFatConfig.h"
//#include "ESP8266SdFat\SdFat.h"
//#include <Adafruit_SPIFlash.h>
#include <Mouse.h>
#include <BME280.h>
#include <BME280I2C.h>
#include <EnvironmentCalculations.h>
#include "baro.h"
#include "Serial.h"
#include "vars.h"
#include "Orientation/Orientation.h"
//#include "imuFilter.h"

//#include "ff.h"
//#include "diskio.h"

#define DISK_LABEL    "EXT FLASH"

//BME280I2C::Settings settings(
//  BME280::OSR_X1,
//  BME280::OSR_X1,
//  BME280::OSR_X1,
//  BME280::Mode_Forced,
//  BME280::StandbyTime_1000ms,
//  BME280::Filter_16,
//  BME280::SpiEnable_False,
//  BME280I2C::I2CAddr_0x76
//);
//
//BME280I2C bme(settings);

//#include "flash_config.h"

//Adafruit_SPIFlash spiflash(&flashTransport);

//Adafruit_SPIFlash flash();

//FatVolume fatfs;

//FATFS elmchamFatfs;

uint8_t workbuf[4096]; // Working buffer for f_fdisk function.

#define FILE_NAME      "datalog.txt"

//#define ADAFRUIT_FLASHTRANSPORT_RP2040_H_
//#define _LFS_LOGLEVEL_          4
//#define FILE_NAME      "datalog.txt"

//bool setRX(4);
//bool setCS(8);
//bool setSCK(2);
//bool setTX(3);

//double Kp = 0.5;
//double Ki = 0;
//double Kd = 0.033;

//Servo parachute;

//File flash;
//SPIFlash exflash(5);

TVCClass TVC(true, true);

baroClass baro;

//File file1;

//PID pidx(&anglex, &anglex1, &Setpoint, Kp, Ki, Kd, DIRECT);
//PID pidz(&anglez, &anglez1, &Setpoint, Kp, Ki, Kd, DIRECT);

Bmi088Accel accel(Wire, 0x18);
Bmi088Gyro gyro(Wire, 0x68);

Madgwick filter;

//LittleFSConfig cfg;
//cfg.setAutoFormat(false);
//LittleFS.setConfig(cfg);

//SPIFlash flash;
//Sd2Card card;
//SdVolume volume;
//SdFile piss;

void setup() {
  Serial.begin(115200);
  Serial.print("angle test");

  addr = startAddr;

  EEPROM.begin(98304);  //98304

  //flashSetup();

  Wire.setSDA(0);
  Wire.setSCL(1);
  Wire.begin();

  //  SPI.setRX(4);
  //  SPI.setTX(3);
  //  SPI.setSCK(2);

  //SPI.begin();
  //SPI.beginTransaction();

  int status;
  status = accel.begin();
  status = gyro.begin();

  filter.begin(100); // update rate in Hz

  oldMillis2 = 5;
  oldMillis3 = 5;

  //pidx.SetMode(AUTOMATIC);
  //pidz.SetMode(AUTOMATIC);

  pinMode(26, INPUT); //vin / adc0

  ledr(0);
  ledg(0);
  ledb(0);

  //  Kp = (EEPROM.read(0));
  //  Ki = (EEPROM.read(1));
  //  Kd = (EEPROM.read(2));

  //  delayPeriod = (EEPROM.read(3)); //backup delay period if no baro (from burnout to ejection)

  //pinMode(pyro1,OUTPUT); //pyro1
  //file1 = SD.open("piss.txt", FILE_WRITE);

  servox.attach(13);
  servoy.attach(14);
  servox.write(90);
  servoy.write(90);

  if (useProp == true) {
    prop.attach(15);
    prop.write(0);
  }
  if (useParachuteServo == true) {
    parachuteServo.attach(15);
    parachuteServo.write(0);
  }
  //parachute.attach(15);
  //parachute.write(0);

  //  parachute.attach(15);
  //  parachute.write(0);

  if (!gyro.begin()) {
    Serial.println("no gyro");
    digitalWrite(18, LOW);
    lastEvent = "no gyro";
    runMode = -1;
  }

  while (!baro.begin()) {
    Serial.println("no baro");
    digitalWrite(18, LOW);
    lastEvent = "no baro";
    runMode = -1;
  }


  //  if (!SD.begin(SDCS)) {
  //    Serial.println("no sd card");
  //    SDAvailable = false;
  //    tone(9, 200, 200);
  //    delay(200);
  //  }

  //LittleFS.begin();

  //  File file = SD.open("datalog.txt", FILE_WRITE);
  //  //File data = LittleFS.open("/data.txt","w+");
  //
  //  file.println();
  //  file.println();
  //  file.println();
  //  file.println();
  //  file.println();
  //  file.close();

  //  if (!SD.begin(PB1)){
  //    Serial.println("No SD card!");
  //    SDCard = false;
  //  }

  //gravity = accel.getAccelY_mss();

  //EEPROM.end();

  delay(200);

  if (baro.alt() <= -4000) {
    watchdog_enable(1, 1);
    while (1);
  }

  float buzTone = 1000;

  //  for (int i = 0; i <= 1000; i+= 1){
  //    float delayP = 2.5;
  //    buzTone -= 1;
  //    tone(9,buzTone,delayP);    //buzzer startup beep
  //    delay(delayP);
  //  }

  tone(9, 300, 200);
  delay(200);
  tone(9, 400, 200);
  delay(200);
  tone(9, 500, 200);

  ledr(1);
  ledg(1);
  groundAlt = baro.alt();
  servox.write(centrepointX - servoLimit);
  delay(gimbalDemoDelayPeriod);
  servox.write(centrepointX);
  delay(gimbalDemoDelayPeriod);
  servox.write(centrepointX + servoLimit);
  delay(gimbalDemoDelayPeriod);
  servox.write(centrepointX);
  delay(gimbalDemoDelayPeriod);
  servoy.write(centrepointY - servoLimit);
  delay(gimbalDemoDelayPeriod);
  servoy.write(centrepointY);
  delay(gimbalDemoDelayPeriod);
  servoy.write(centrepointY + servoLimit);
  delay(gimbalDemoDelayPeriod);
  ledr(0);
  delay(100);
  servoy.write(90);
  ledg(0);
  servox.write(centrepointX);
  servoy.write(centrepointY);
  EEPROM.end();
  booted = true;
}

void loop() {
  //rp2040.idleOtherCore();
  accel.readSensor();
  gyro.readSensor();
  TVC.estimateAngles(runMode, imuGain, accel.getAccelX_mss(), accel.getAccelY_mss(), accel.getAccelZ_mss(), gyro.getGyroX_rads(), gyro.getGyroY_rads(), gyro.getGyroZ_rads());

  anglex = TVC.pitch();
  angley = TVC.roll();
  anglez = TVC.yaw();

  currMillis = millis();
  cycleTime = (currMillis - oldMillis2);
  oldMillis2 = millis();

  flightTime = (millis() - ignitionTime) / 1000;

  ax = accel.getAccelX_mss();
  ay = accel.getAccelY_mss();
  az = accel.getAccelZ_mss();
  gx = gyro.getGyroX_rads();
  gy = gyro.getGyroY_rads();
  gz = gyro.getGyroZ_rads();
  Vin = vin();

  accelSpeedy = (((accelSpeedy + (accel.getAccelY_mss())) - gravity));
  accelAlt = (accelAlt + accelSpeedy);

  baro.computeBaro();
  vSpeed = baro.baroVel();
  Alt = baro.alt();
  smoothedalt = baro.smoothedAlt();

  vspeed = vSpeed;
  servoanglex = servoAnglex();
  servoanglez = servoAnglez();

  //rp2040.idleOtherCore();

  datalogString = (String(currMillis) + ": " + String(flightTime) + " " + String(runMode) + " " + String(TVC.pitch()) + " " + String(TVC.roll()) + " " + String(TVC.yaw()) + " " + String(servoanglex - centrepointX) + " " + String(servoanglez - centrepointY) + " " + "alt:" + " " + String(Alt) + " " + String(smoothedalt) + " " + String(vSpeed) + " nav: " + String(TVC.accelz()) + " " + String(TVC.accelzSpeed()) + " " + String(TVC.accelAlt()) + " vin: " + String(Vin) + " " + "raw accel readings:" + " " + String(ax) + " " + String(ay) + " " + String(az) + " filtered az: " + String(TVC.filteredAccelY()) + " " + "gyro:" + " " + String(gx * RAD_TO_DEG) + " " + String(gy * RAD_TO_DEG) + " " + String(gz * RAD_TO_DEG) + " " + String(cycleTime) + " " + lastEvent);
  //datalogString = String(gx * RAD_TO_DEG) + " " + String(gy * RAD_TO_DEG) + " " + String(gz * RAD_TO_DEG);
  //datalogString = (String(TVC.pitch()) + " " + String(TVC.roll()) + " " + String(TVC.yaw()));

  //  telem.currMillis = currMillis;
  //  telem.runMode = runMode;
  //  telem.Anglex = anglex;
  //  telem.Angley = angley;
  //  telem.Anglez = anglez;
  //  telem.servoanglex = servoanglex - 90;
  //  telem.servoanglez = servoanglez - 90;
  //  telem.Alt = Alt;
  //  telem.smoothedalt = smoothedalt;
  //  telem.vSpeed = vSpeed;
  //  telem.Vin = Vin;
  //  telem.ax = ax;
  //  telem.ay = ay;
  //  telem.az = az;
  //  telem.gx = gx;
  //  telem.gy = gy;
  //  telem.gz = gz;
  //  telem.cycleTime = cycleTime;
  //  telem.lastEvent = lastEvent;

  //rp2040.resumeOtherCore();

  //  anglex = (anglex + (gyro.getGyroX_rads() * (M_PI / 180) * ((4078/71) * 1.5)));
  //  angley = (angley + (gyro.getGyroY_rads() * (M_PI / 180) * ((4078/71) * 1.5)));
  //  anglez = (anglez + (gyro.getGyroZ_rads() * (M_PI / 180) * ((4078/71) * 1.5)));

  //  anglex = (((anglex + (gyro.getGyroX_rads())) * 4068) /71);
  //  angley = (((anglex + (gyro.getGyroX_rads())) * 4068) /71);
  //  anglez = (((anglex + (gyro.getGyroX_rads())) * 4068) /71);

  if (datalogging == true) {
    //exFlashDatalog();
    //flashDatalog();
    //    rp2040.fifo.push(1);
    //    rp2040.fifo.push(currMillis);
    //    rp2040.fifo.push(anglex);
    //    rp2040.fifo.push(angley);
    //    rp2040.fifo.push(anglez);
    //    rp2040.fifo.push(servoAnglex() - centrepoint);
    //    rp2040.fifo.push(servoAnglez() - centrepoint);
    //    rp2040.fifo.push(baro.alt());
    //    rp2040.fifo.push(baro.smoothedAlt());
    //    rp2040.fifo.push(vSpeed);
    //    rp2040.fifo.push(vin());
    //    rp2040.fifo.push(ax);
    //    rp2040.fifo.push(ay);
    //    rp2040.fifo.push(az);
    //    rp2040.fifo.push(gx);
    //    rp2040.fifo.push(gy);
    //    rp2040.fifo.push(gz);
  }

  if (Serial.available()) {
    serialInput = Serial.readString();
  }

  if (serialInput != "") {
    processSerial(serialInput);
    serialInput = "";
  }

  //rp2040.idleOtherCore();
  //  if (BOOTSEL) {
  //    buz(1);
  //    runMode = 4;
  //  }
  //  if (!BOOTSEL) {
  //    buz(0);
  //  }
  //rp2040.resumeOtherCore();

  //runmodes
  if (runMode == -5) {
    gimbalDemo();
  } else if (runMode == -4) {
    activeGimbalDemo();
  } else if (runMode == -3) {
    countdown();
  } else if (runMode == -2) { //cli mode
    //cli();
    //cmd();
  } else if (runMode == -1) { //error 1

  } else if (runMode == 0) {
    wait();
  } else if (runMode == 1) {
    poweredAscent();
  } else if (runMode == 2) {
    coast();
  } else if (runMode == 3) {
    descent();
  } else if (runMode == 4) {
    //runMode = 0;
    //rp2040.reboot(); //reboot in case of accidental launch detect or multiple flights
    landed();
  } else if (runMode == 69) {
    gimbalTest();
  }

  //  Serial.println(baro.alt());
  if (runMode >= 0) {
    //SPI.transfer(baro.alt());
    //Serial.println(EEPROM.length());
    //    Serial.print(anglex);
    //    Serial.print("     ");
    //    Serial.print(angley);
    //    Serial.print("     ");
    //    Serial.print(anglez);
    //    Serial.print("     ");
    //    //Serial.print(cycleTime);
    //    //Serial.print("     ");
    //    //Serial.print(accelSpeedy);
    //    //Serial.print("     ");
    //    //Serial.print(accelAlt);
    //    Serial.print(servoAnglex() - centrepoint);
    //    Serial.print("     ");
    //    Serial.print(servoAnglez() - centrepoint);
    //    Serial.print("     ");
    //    Serial.print("alt: ");
    //    Serial.print("     ");
    //    Serial.print(baro.alt());
    //    Serial.print("     ");
    //    Serial.print(baro.smoothedAlt());
    //    Serial.print("     ");
    //    Serial.print(vSpeed);
    //    Serial.print("     ");
    //    Serial.print(vin());
    //    Serial.print("     ");
    //    Serial.print(cycleTime);
    //    Serial.print("     ");
    //    Serial.print(datalogString);
    //    Serial.println();
  }

  //  if (SDCard == true){
  //    file1.print(anglex);
  //    file1.print("     ");
  //    file1.print(anglez);
  //    file1.print("     ");
  //    file1.print(servoAnglex());
  //    file1.print("     ");
  //    file1.println(servoAnglez());
  //  }

  //  Serial.print(accel.getAccelX_mss());
  //  Serial.print("     ");
  //  Serial.print(accel.getAccelY_mss());
  //  Serial.print("     ");
  //  Serial.println(accel.getAccelZ_mss());

  //Y axis is up/down

  //Serial.println(gyro.getGyroX_rads());
  //pidx.Compute();
  //pidz.Compute();

  //servoAnglex = anglex1 + 70;
  //servoAnglez = anglez1 + 70;
  //oldMillis2 = currMillis;
  //oldMillis3 = currMillis;
  //delay(100);
}

void setup1() {
  //ESPSerial.begin(38400);
  //  SPI.setRX(4);
  //  SPI.setTX(3);
  //  SPI.setSCK(2);
  //
  //  SPI.begin();
  //
  SPISetup();
  //exFlashSetup();
  SDSetup();
  flashSetup();

  //telemSetup(8);

  if (LittleFS.exists("/config.txt")) {
    File file = LittleFS.open("/config.txt", "r");
    Kp = file.parseFloat();
    Ki = file.parseFloat();
    Kd = file.parseFloat();
    delayPeriod = file.parseFloat();
    file.close();
  }
  else {
    File file = LittleFS.open("/config.txt", "a");
    file.println(defaultP);
    file.println(defaultI);
    file.println(defaultD);
    file.println(defaultDelay);
    file.close();
    Kp = defaultP;
    Ki = defaultI;
    Kd = defaultD;
    delayPeriod = defaultDelay;
  }

  //  while (BOOTSEL){
  //    runMode = 0; //set runmode to "waiting" if bootsel pressed (can be used for arming)
  //  }

  //  EEPROM.begin(98304);
  //  Kp = (EEPROM.read(0));
  //  Ki = (EEPROM.read(1));
  //  Kd = (EEPROM.read(2));
  //
  //  delayPeriod = (EEPROM.read(3)); //backup delay period if no baro (from burnout to ejection)
  //
  //
  //  if (!SD.begin(SDCS)){
  //    Serial.println("no sd card");
  //    SDAvailable = false;
  //    tone(9,200,200);
  //    delay(200);
  //  }
  //
  //  File file = SD.open("datalog.txt", FILE_WRITE);
  //  File data = LittleFS.open("/data.txt","w+");
  //
  //  file.println();
  //  file.println();
  //  file.println();
  //  file.println();
  //  file.println();
  //  file.close();
}

byte fifo;

void loop1() {

  //servoanglex();
  //servoangley();

  if (runMode == -2) {
    cmd();
  }
  //ESPSerial.println(datalogString);
  if (runMode >= 0) {
    Serial.println(datalogString); //has to be on the second core since if it's on the first core that somehow breaks estimateAngles();
    //    if (ESPSerial.available()){
    //      Serial.write(ESPSerial.read());
    //    }
  }
  ESP.send(datalogString);

  String SPIInput = ESP.read();
  static String oldSPIInput;
  if (SPIInput.length() > 0 & oldSPIInput != SPIInput) {
    SPIInput.trim();
    //Serial.println(SPIInput);
    oldSPIInput = SPIInput;
    //serialInput = "";
  }

  if (SPIInput != "") {
    processSerial(SPIInput);
    SPIInput = "";
  }

  //int ESPMessageSize = sizeof(datalogString);
  //char ESPMessage[ESPMessageSize] = datalogString;
  //ESPSerial.println(datalogString);
  //  int num1 = serialInput.parseInt();
  //  int num2 = serialInput.parseInt();
  //  if ((num1 != 0) & (num2 != 0)){
  //
  //  }
  //telemSend();
  //  if (serialInput == "formatExflash"){
  //    SerialFlash.eraseAll();
  //  }
  //  if (runMode == 3) {
  //    static boolean savedTelem = false;
  //    if (savedTelem == false) {
  //      File32 exflash = fatfs.open("datalog.txt", FILE_READ);
  //      File flash = LittleFS.open("/data.txt", "a");
  //      while (exflash.available()) {
  //        flash.write(exflash.read());
  //      }
  //      flash.close();
  //      exflash.close();
  //      fatfs.rmdir("/");
  //      savedTelem == true;
  //    }
  //  }
  //  if (runMode == 4) {
  //    static boolean savedTelem = false;
  //    if (savedTelem == false) {
  //      File32 exflash = fatfs.open("datalog.txt", FILE_READ);
  //      File flash = LittleFS.open("/data.txt", "a");
  //      while (exflash.available()) {
  //        flash.write(exflash.read());
  //      }
  //      flash.close();
  //      exflash.close();
  //      fatfs.rmdir("/");
  //      savedTelem == true;
  //    }
  //  }

  //  if (ESPSerial.available()) {
  //    if (!isDigit(ESPSerial.peek())) {
  //      serialInput = ESPSerial.readString();
  //      serialInput.trim();
  //    }
  //  }


  if (runMode >= 0) {
    if (datalogging == true) {
      datalog();
      //exFlashDatalog();
      if (logToFlash == true) {
        flashDatalog();
      }
      if (logToSD == true) {
        SDDatalog();
      }
    }
    if (datalogging == false) {
      //data.close();
    }
  }
  //  if (runMode == 3) {
  //    parachute.write(180);
  //  }
  //  if (runMode != 3) {
  //    parachute.write(0);
  //  }
}

void cmd() {
  ledr(1);
  ledg(1);
  ledb(1);
  //Serial.println(ESP.read());
}

void SPISetup() {
  SPI.setRX(4);
  SPI.setTX(3);
  SPI.setSCK(2);
  //SPI.beginTransaction(SPISettings(10000000, LSBFIRST, SPI_MODE0));
  SPI.begin();
}

//void exFlashSetup() {
//  //flash.begin();
//  if (!spiflash.begin()) {
//    Serial.println("flash error");
//  }
//  if (!fatfs.begin(&spiflash)) {
//    Serial.println("SPI flash partition error for some reason");
//    formatExternalFlash();
//    rp2040.reboot();
//  }
//  else {
//    Serial.println("spi flash init done");
//  }
//  File32 exflash = fatfs.open("datalog.txt", FILE_WRITE);
//  exflash.println();
//  exflash.println();
//  exflash.println();
//  exflash.println();
//  exflash.println();
//  exflash.close();-
//}

void SDSetup() {
  if (!SD.begin(SDCS)) {
    Serial.println("no sd card");
    SDAvailable = false;
    tone(9, 200, 200);
    delay(200);
  }
  if (autoLogging == true) {
    if (SDAvailable == true) {
      logToSD = true;
      logToFlash = false;
    } else {
      logToSD = false;
      logToFlash = true;
    }
  }
  if (logToSD == true) {
    File file = SD.open("datalog.txt", FILE_WRITE);
    file.println();
    file.println();
    file.println();
    file.println();
    file.println();
    file.close();
  }
  if (SD.exists("config.txt")) {
    LittleFS.remove("config.txt");
    File file = SD.open("config.txt", FILE_READ);
    File flash = LittleFS.open("config.txt", "a");
    while (file.available()) {
      flash.write(file.read());
    }
    file.close();
    flash.close();
    SD.remove("config.txt");
    rp2040.reboot();
  }
}

void flashSetup() {
  LittleFS.begin();
  File flash = LittleFS.open("/data.txt", "a");
  if (flash) {
    if (logToFlash == true) {
      flash.println();
      flash.println();
      flash.println();
      flash.println();
      flash.println();
      flash.close();
    }
  }
  else {
    Serial.println("littlefs error");
  }
}

void flashtoSD() {
  File file = SD.open("datalog.txt", FILE_WRITE);
  File flash = LittleFS.open("data.txt", "r");
  while (flash.available()) {
    file.write(flash.read());
  }
  //  while (fifo != -1) {
  //file.write(rp2040.fifo.pop());
  //file.write(fifo);
  //Serial.println("pop");
  //  }
  file.close();
  flash.close();
  Serial.println("Copied all data from internal QPSI flash to the MicroSD card");
  Serial.println("done");
}
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

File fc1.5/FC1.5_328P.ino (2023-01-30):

#include <EEPROM.h>
//#include <SD.h>
//#include <SPIMemory.h>
//#include <PID_v1.h>
#include <SPI.h>
#include <EnvironmentCalculations.h>
#include <BME280I2C.h>
#include <Servo.h>
#include "BMI088.h" 

float servoLimit = 10; //servo actuation limit on either side e.g. 10deg = 10deg on either side = 20deg total
float centrepoint = 0; //servo centrepoint,usually 90

double Kp = 0.1;  // PID loop values
double Ki = 0;
double Kd = 0.033;
//double Setpoint = 90;

float targetAnglex = 0;
float targetAnglez = 0;

float delayPeriod = 3; //backup delay period if no baro (from burnout to ejection)

float gyroThreshold = 0.1; //threshold for speed of rotation to detect landing

float gravity = 9.73; //gravity
float offset1;

float referencePressure = 1018.6;  // hPa local QFF (official meteor-station reading)
float outdoorTemp = 25;           // °C  measured local outdoor temp.
float barometerAltitude = 1650.3;  // meters ... map readings + barometer position

double anglex;
double angley;
double anglez;
//double servoAnglex;
//double servoAnglez;
double anglex1;
double anglez1;
float accelSpeedy;
float accelAlt;
float oldMillis2;
float oldMillis3;
float cycleTime;
int runMode = 0;
int altcount = 0;
float altitude;
unsigned long currMillis;
unsigned long oldMillis;
const int SDCS = PB1;
boolean SDCard = true;

Servo servox;
Servo servoy;

//File file1;

//PID pidx(&anglex, &anglex1, &Setpoint, Kp, Ki, Kd, DIRECT);
//PID pidz(&anglez, &anglez1, &Setpoint, Kp, Ki, Kd, DIRECT);

Bmi088Accel accel(Wire,0x18);
Bmi088Gyro gyro(Wire,0x68);

BME280I2C::Settings settings(
   BME280::OSR_X1,
   BME280::OSR_X1,
   BME280::OSR_X1,
   BME280::Mode_Forced,
   BME280::StandbyTime_1000ms,
   BME280::Filter_16,
   BME280::SpiEnable_False,
   BME280I2C::I2CAddr_0x76
);

BME280I2C bme(settings);
//SPIFlash flash;
//Sd2Card card;
//SdVolume volume;
//SdFile piss;

void setup() {
  int status;
  status = accel.begin();
  status = gyro.begin();
  Serial.begin(115200);
  Serial.print("angle test");
  Wire.begin();

  oldMillis2 = 5;
  oldMillis3 = 5;
  
  //pidx.SetMode(AUTOMATIC);
  //pidz.SetMode(AUTOMATIC);

  pinMode(PB0,OUTPUT); //pyro1
  //file1 = SD.open("piss.txt", FILE_WRITE);
  
  servox.attach(PD5);
  servoy.attach(PD6);
  servox.write(90);
  servoy.write(90);
    if (!gyro.begin()){
    Serial.println("no gyro");
    while(1);
  }

  while (!bme.begin()){
    Serial.println("no baro");
    while(1);
  }
  
//  if (!SD.begin(PB1)){
//    Serial.println("No SD card!");
//    SDCard = false;
//  }

  //gravity = accel.getAccelY_mss();
  
  delay(200);
  servox.write(80);
  delay(100);
  servox.write(90);
  delay(100);
  servox.write(100);
  delay(100);
  servox.write(90);
  delay(100);
  servoy.write(80);
  delay(100);
  servoy.write(90);
  delay(100);
  servoy.write(100);
  delay(100);
  servoy.write(90);
}

void loop() {
  currMillis = millis();
  cycleTime = (currMillis - oldMillis2);
  accel.readSensor();
  gyro.readSensor();

  accelSpeedy = (((accelSpeedy + (accel.getAccelY_mss())) - gravity));
  accelAlt = (accelAlt + accelSpeedy);
    
//  anglex = (anglex + (gyro.getGyroX_rads() * (M_PI / 180) * ((4078/71) * 1.5)));
//  angley = (angley + (gyro.getGyroY_rads() * (M_PI / 180) * ((4078/71) * 1.5)));
//  anglez = (anglez + (gyro.getGyroZ_rads() * (M_PI / 180) * ((4078/71) * 1.5)));

  anglex = (anglex + (gyro.getGyroX_rads() * (M_PI / 180) * ((4078/71) * (cycleTime / 10))));
  angley = (angley + (gyro.getGyroY_rads() * (M_PI / 180) * ((4078/71) * (cycleTime / 10))));
  anglez = (anglez + (gyro.getGyroZ_rads() * (M_PI / 180) * ((4078/71) * (cycleTime / 10))));

//  anglex = (((anglex + (gyro.getGyroX_rads())) * 4068) /71);
//  angley = (((anglex + (gyro.getGyroX_rads())) * 4068) /71);
//  anglez = (((anglex + (gyro.getGyroX_rads())) * 4068) /71);
  
  if (runMode == 0){
    wait();
  }
  if (runMode == 1){
    poweredAscent();
  }
  if (runMode == 2){
    coast();
  }
  if (runMode == 3){
    descent();
  }
  if (runMode == 4){
    landed();
  }
  
//  Serial.println(alt());

  Serial.print(anglex);
  Serial.print("     ");
  Serial.print(angley);
  Serial.print("     ");
  Serial.print(anglez);
  Serial.print("     ");
  //Serial.print(alt());
  //Serial.print("     ");
  //Serial.print(cycleTime);
  //Serial.print("     ");
  //Serial.print(accelSpeedy);
  //Serial.print("     ");
  //Serial.print(accelAlt);
  Serial.print(servoAnglex());
  Serial.print("     ");
  Serial.print(servoAnglez());
  Serial.print("     ");

//  if (SDCard == true){
//    file1.print(anglex);
//    file1.print("     ");
//    file1.print(anglez);
//    file1.print("     ");
//    file1.print(servoAnglex());
//    file1.print("     ");
//    file1.println(servoAnglez());
//  }

//  Serial.print(accel.getAccelX_mss());
//  Serial.print("     ");
//  Serial.print(accel.getAccelY_mss());
//  Serial.print("     ");
//  Serial.println(accel.getAccelZ_mss());

 //Y axis is up/down
 
  //Serial.println(gyro.getGyroX_rads());
  //pidx.Compute();
  //pidz.Compute();
  
  //servoAnglex = anglex1 + 70;
  //servoAnglez = anglez1 + 70;
  oldMillis2 = currMillis;
  oldMillis3 = currMillis;
  Serial.println();
  delay(10);
}

void wait(){
  boolean foundGravity = false;
  if (foundGravity == false){
    offset1 = (accel.getAccelY_mss() - gravity);
    foundGravity = true;
  }
  Serial.println("waiting on pad");
  anglex = 0;
  angley = 0;
  anglez = 0; // prevent gyro drift while waiting on pad
  //servoAnglex = 90;
  //servoAnglez = 90;
  accelSpeedy = 0;

  if (accel.getAccelY_mss() >= 11) {
    Serial.println("powered ascent");
    runMode = 1;
  }
}

void poweredAscent() {
  servox.write(servoAnglex);
  servoy.write(servoAnglez);

  if (accel.getAccelY_mss() <= 7) {
    servox.write(90);
    servoy.write(90); //homes and locks servos
    Serial.println("coasting");
    oldMillis = currMillis;
    runMode = 2;
  }
}

void coast() {
  float altitude2 = alt();
  altcount += 1;
  //Serial.println(altcount);
  //delay(500);
  //if (altcount >=delayPeriod / 2)
  if ((alt() <= (altitude2 - 0.05)) or ((currMillis - oldMillis) >= (delayPeriod * 1000))){
    Serial.println("descending");
    oldMillis = currMillis;
    runMode = 3;
  }
}

void descent() {
  digitalWrite(PB0,HIGH);//pyro charge 1
  if ((gyro.getGyroX_rads() <= gyroThreshold) & (gyro.getGyroY_rads() <= gyroThreshold) & (gyro.getGyroZ_rads() <= gyroThreshold) & (gyro.getGyroX_rads() >= -gyroThreshold) & (gyro.getGyroY_rads() >= -gyroThreshold) & (gyro.getGyroZ_rads() >= -gyroThreshold)) {
    Serial.println("landed!");
    runMode = 4;
  }
}

void landed() {
}

//custom libraries
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

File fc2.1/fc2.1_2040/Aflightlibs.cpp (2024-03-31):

#include "Aflightlibs.h"
#include "Arduino.h"
#include <SerialFlash.h>
#include "imuFilter.h"
#include "Orientation/Orientation.h"
#include "Orientation/Quaternion.h"
#include "Orientation/Orientation.cpp"
#include "Orientation/Quaternion.cpp"
#include "math.h"
//#include "vars.h"
//#define GET_FIELD(regname,value) ((value & regname##_MASK) >> regname##_POS)
//#define  SET_FIELD(regval,regname,value) ((regval & ~regname##_MASK) | ((value << regname##_POS) & regname##_MASK))

//LittleFSConfig cfg;
//cfg.setAutoFormat(false);
//LittleFS.setConfig(cfg);

float x, y, z;
float _pitch, _roll, _yaw;
float accelZ; //
float pyroTime = 250; //time for pyro channel to stay on
float pyroPin1 = 10;
float pyroPin2 = 11;
float pyroPin3 = 12;
float filteredaccely;
float accelalt;
float accelspeedz;
float _gravity;
boolean LEDEN, BUZEN;

float _Kp = 30.0;
float _Ki = 0.0;

uint64_t thisLoopMicros = 0; // Stores microsecond timestamp for current loop
uint64_t lastOriUpdate = 0; // Stores mircosecond timestamp for last time orientation updated

struct quaternion {
  float r;    /* real bit */
  float x, y, z;  /* imaginary bits */
};

quaternion masterQuaternion;
quaternion tempQuaternion;
float angX, angY, angZ;

float q[4] = {1.0, 0.0, 0.0, 0.0};

imuFilter quat;

Orientation ori; // Main orientation measurement
EulerAngles oriMeasure; // Quaternion converted to Euler Angles for maths etc.

//TVCClass::TVCClass(void){}

TVCClass::TVCClass() {
  LEDEN = true;
  BUZEN = true;
  pinMode(10, OUTPUT); //pyros
  pinMode(11, OUTPUT);
  pinMode(12, OUTPUT);

  pinMode(18, OUTPUT); //leds
  pinMode(19, OUTPUT);
  pinMode(20, OUTPUT);
  thisLoopMicros = lastOriUpdate = micros(); // Set starting time after init/calibration
  quat.setup();
}

TVCClass::TVCClass(boolean _LEDEN, boolean _BUZEN) {
  LEDEN = _LEDEN;
  BUZEN = _BUZEN;
  pinMode(10, OUTPUT); //pyros
  pinMode(11, OUTPUT);
  pinMode(12, OUTPUT);

  pinMode(18, OUTPUT); //leds
  pinMode(19, OUTPUT);
  pinMode(20, OUTPUT);
  thisLoopMicros = lastOriUpdate = micros(); // Set starting time after init/calibration
  quat.setup();
}

void TVCClass::pyro1() {
  static int olderMillis = millis();
  static boolean fired = false;
  digitalWrite(pyroPin1, HIGH);
  if (millis() - olderMillis >= pyroTime) {
    if (fired == false) {
      digitalWrite(pyroPin1, LOW);
      fired = true;
    }
  }
}

void TVCClass::pyro2() {
  static int olderMillis = millis();
  static boolean fired = false;
  digitalWrite(pyroPin2, HIGH);
  if (millis() - olderMillis >= pyroTime) {
    if (fired == false) {
      digitalWrite(pyroPin2, LOW);
      fired = true;
    }
  }
}

void TVCClass::pyro3() {
  static int olderMillis = millis();
  static boolean fired = false;
  digitalWrite(pyroPin3, HIGH);
  if (millis() - olderMillis >= pyroTime) {
    if (fired == false) {
      digitalWrite(pyroPin3, LOW);
      fired = true;
    }
  }
}

float TVCClass::anglex() {
  return _yaw;
}

float TVCClass::angley() {
  return _roll;
}

float TVCClass::anglez() {
  return _pitch;
}

float TVCClass::pitch() {
  return _pitch;
}

float TVCClass::roll() {
  return _roll;
}

float TVCClass::yaw() {
  return _yaw;
}

float TVCClass::filteredAccelY() {
  return filteredaccely;
}

float TVCClass::accelz() {
  return accelZ;
}

float TVCClass::accelAlt() {
  return accelalt;
}

float TVCClass::accelzSpeed() {
  return accelspeedz;
}
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

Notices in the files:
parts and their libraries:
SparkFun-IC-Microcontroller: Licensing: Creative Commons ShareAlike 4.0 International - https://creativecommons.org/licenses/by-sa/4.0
